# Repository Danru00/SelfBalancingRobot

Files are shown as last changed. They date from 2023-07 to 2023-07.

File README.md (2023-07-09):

# SelfBalancingRobot
Two-wheeled self-balancing robot realized for the Robotics course at Polito, academic year 2022-2023. The simulation is based on ROS Noetic and works on Ubuntu 20.04

# Run the Gazebo simulation
- Download the robot_assembly folder in your catkin workspace and run from a terminal: catkin_make
- Run from a terminal: roslaunch robot_assembly istagger_launch.launch
- After starting the simulation, the robot will initially fall. By rotating it upwards the PID controller will start working balancing the robot as prescribed
- You can tune the PID parameter by changing them in the Python file "pid_controller" under robot_assembly/src

# Run the Simscape simulation
- Download the Simscape folder
- Run the robot_assembly_simscape_DataFile in Matlab
- Open and run the robot_assembly.slx file to start the simulation
- You can tune the PID parameters changing them in the PID block

# Hardware implementation and Arduino code
Hardware details together with additional information on the project can be found in the Report_RoboticsProject_SelfBalancingRobot.pdf included in this repo.

The Arduino code can be uploaded through the Arduino IDE software and is intended for use on the Arduino Nano, but should also work with other similar boards. To correctly compile the program it is necessary to install the libraries linked at the beginning of the code by downloading them from GitHub and putting them under the Documents/Arduino/libraries folder.

Pin definitions in the code have to be changed depending on the connections with the driver and the motor. The IMU calibration offsets, PID parameters, and the unstable equilibrium position used for reference can also be changed in the program depending on the adopted hardware configuration.

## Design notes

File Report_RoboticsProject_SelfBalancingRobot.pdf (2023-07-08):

# POLITECNICO DI TORINO

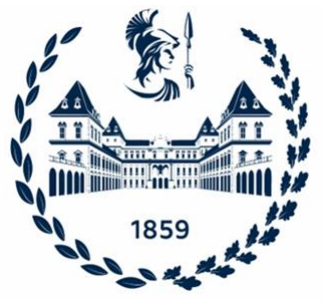
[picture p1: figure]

## Department of CONTROL AND COMPUTER

## ENGINEERING (DAUIN) Master Degree in Mechatronic Engineering

a.a. 2022/2023

## Robotics

## Prof. A. Rizzo

## T.A.: G. Galati and M. Rinaldi

## Self-balancing robot

## Aisa Filippo – 315421

## Musio Maria Grazia – 315756

## Russo Daniele – 308291

## Ursi Mariateresa – 315428

## Valenziano Gaia – 309918

## Contents

## Abstract

This project was aimed to design, simulate, build and study a self-balancing robot.
It is a two wheeled machine which stays in an unstable equilibrium and it returns to it after the application of a disturbance.

The research development started with a first theoretical and simplified model of the system. Then, a detailed and precise CAD model of the robot was created in SolidWorks.
Many simulations were performed: at first in Simscape to visualise the behaviour of the system; later, as soon as the performances were satisfactory, the robot was simulated in Gazebo and finally it was physically built.

The main trouble when designing a robot of this kind was the control system.
In this project a PID controller was chosen to implement a simple but effective and efficient control algorithm. The prototype was built with an IMU element to include a state estimation, which is important for the control system itself.

## Introduction

## Background

The working principle of a two wheeled self-balancing robot is similar to that of the human body, which can be seen as an inverted pendulum balancing the whole upper body around the ankles.
Although the self-balancing robots have advantages with respect to other robotic configurations, e.g. the mechanical simplicity, an accurate control could be very hard to be successfully achieved.

In order to maintain a balance, a gyroscope and accelerometer in form of Inertial Measurement Unit (IMU) is used. The latter provides the angle of fall of the robot that is then used by the PID controller to calculate the motor input required to track the constant reference angle corresponding to the unstable equilibrium position.
The signal is sent as PWM to the motors, increasing and decreasing the speed of the wheels and changing their directions when needed.

Inverted pendulum applications are plenty: in the recent decade, segways making use of bodily movements for steering have emerged on the market.
All these applications share with each other the position of the centre of mass above their pivot points, thus the requirement of active control for balancing.

## Purpose

The focus of this project is to build a simple working prototype of a two wheeled self-balancing robot, starting from the design of its mechanical structure and finishing with the code implementation that enables it to be balanced, at the end.

## Method

At the beginning preliminary research was conducted to correctly understand the system dynamics and the electronics behind. Thus, the dynamic equations were derived.
These equations were used to design a PID controller for stabilising the robot.
Once the model was precisely created in SolidWorks, it was exported and integrated in simulation platforms to emulate the real robot’s behaviour together with the developed control system before the effective construction.

## Theoretical approach

## System modelling

A self-balancing robot is typically modelled as an inverted pendulum.
In this project an even simple model was used at the beginning: an inverted pendulum which was balanced in the unstable equilibrium point through a PID controller.

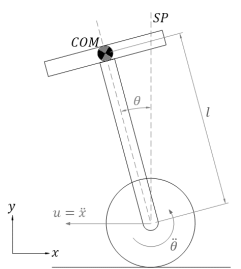
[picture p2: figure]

The equation of motion of the self-balancing robot was derived using Lagrange’s equations (inverted pendulum), by analysing the dynamics of the robot:

lθ¨ − gsinθ = x¨cosθ

Here, l is the distance of the center of mass of the robot from the axis of rotation (i.e. wheel centre), g is the acceleration due to gravity, θ is the pitch angle, θ¨ is the angular acceleration and x¨ is the linear acceleration (fed as control input u).

Then, the dynamics of the model was written as:

θ¨ =

g
l

sinθ +

u
l

cosθ

The state of the system was represented:
{

x1 = θ
x2 = θ˙

; x = [

x1
x2

]=[

θ
θ˙

]

Measuring the pitch angle θ of the robot:

output: y = θ

Figure 1 Dynamics of a Self-Balancing Robot

The control signal influenced the linear acceleration of the base of the robot, therefore:

control signal: u = x¨

Hence, we obtained the open-loop system dynamics:

x¨ = f(x, u) = [

θ˙
θ̈

] = [

x2
g
l

sinθ +

u
l

cosθ]; y = ℎ(x) = x1.

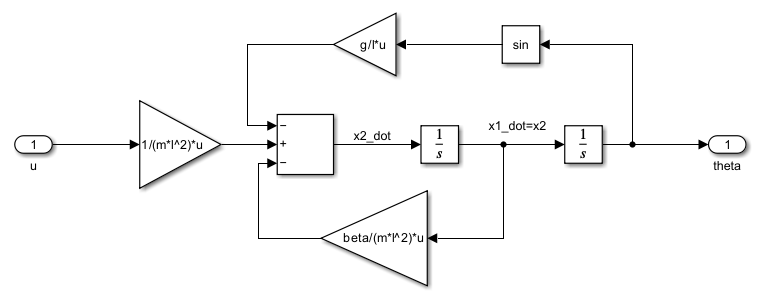
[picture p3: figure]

## Control system

As previously discussed, the control system was based on a PID controller.
It was chosen among many options, which also included LQ and MPC controllers, thanks to its simplicity and the ability to stabilise a system with a high unstable dynamic, maintaining the vertical position of the robot.

Figure 2 Dynamical system in Simulink

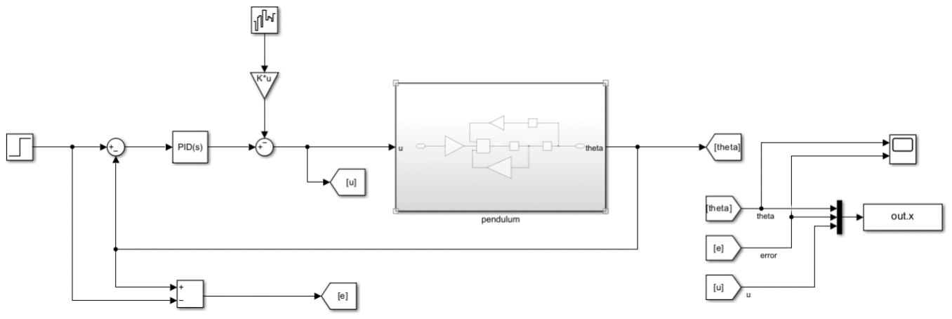
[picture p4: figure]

Figure 3 Closed-loop with PID controller

The primary objective of the PID controller is to maintain the value of the pitch angle θ of the robot close to the setpoint value, chosen to be 180° based on the IMU position on the robot, which is fed to the controller as a reference signal.
The error e(t) is computed through negative feedback, subtracting the feedback measurement from the setpoint. Thus, it is fed as input to the PID controller.
On the basis of Ki, Kp, and Kd controller gains, the input of the plant u(t) was computed:

u(t) = Kp ∗ e(t) + Ki ∗ ∫ e(t)dt

t

0

+

Kd ∗ de(t)
dt

The three control branches are weighted thanks to their gains and then summed together in order to achieve the required input of the plant.

The following explanation clarify the method used to tune those gains:
- Kp, the main task of the proportional part is to reduce the rise time, as well as the steady state error, but it increases the overshoot and generates an offset error;
- Kd, the derivative term increasesthe damping of the system by reducing the overshoot and the settling time, useful to smooth the behaviour of the system;
- Ki, the integral term is used to completely eliminate the steady state error, so it is useful when an offset error is generated by the system.
To summarise, the proportional term corrects the current errors, the integral term compensates the past errors, the derivative term avoids the future errors predicting them.

Tuning the PID controller gains is not done through any formula, but it is an empirical procedure based on the system behaviour, following a conventional order: proportional, integral and derivative, respectively. Hence, the integral removes the offset error generated by the proportional and the derivative smooths the system behaviour.
To reach a correct stabilisation, the tuning was done with the trial and error method on the Simscape simulation and then it was applied to the real robot.

## Simulation

At first the model of the robot was realized in SolidWorks and then exported through a plugin to use it in Matlab and perform the simulation through Simscape.
Moreover, the same CAD model was exported in URDF format through another plugin to be uploaded in ROS and simulated in Gazebo.

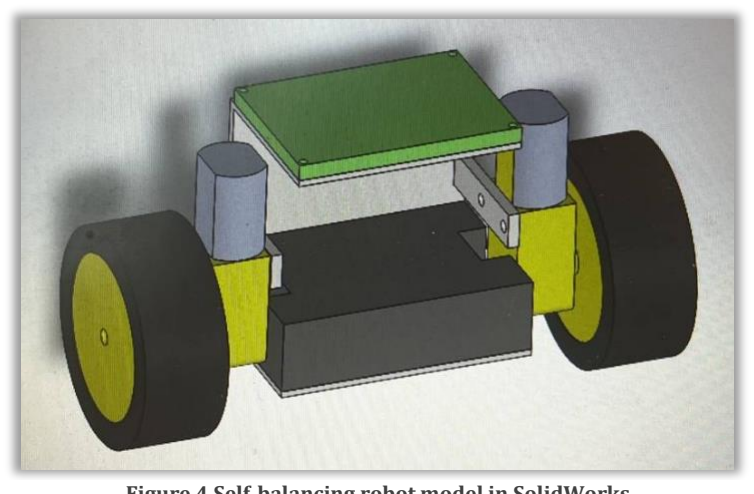
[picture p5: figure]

## Simulink and Simscape

Simscape is part of the larger MATLAB and Simulink software environment and uses a physical modelling approach to represent and simulate systems. It allows users to model and simulate a wide range of physical systems, including mechanical, electrical, hydraulic and thermal systems. It provides a library of pre-built components, such as motors, sensors, and actuators, that can be easily combined to create complex systems.
The simulation can be run and analysed using Simulink tools, such as scopes and data logging. Simscape also provides tools for analysing system performance, such as frequency response plots and transient analysis.

Our self-balancing robot was simulated in Simscape with the 3D CAD model of the real robot. Taking inspiration from other projects, the simulation was performed in Simscape by integrating the robot file obtained through the Simscape Multibody Link Simulink blocks to implement the control.

Thus, a PID controller was inserted and properly tuned. After, an initial perturbation was inserted to check the stability of the robot.

At the beginning, small arbitrary values were set as PID parameters to observe the behaviour in response to an applied disturbance. Then, step by step we tuned them, until the convergence to the equilibrium was achieved. The final values are shown in Figure 7.

Figure 4 Self-balancing robot model in SolidWorks

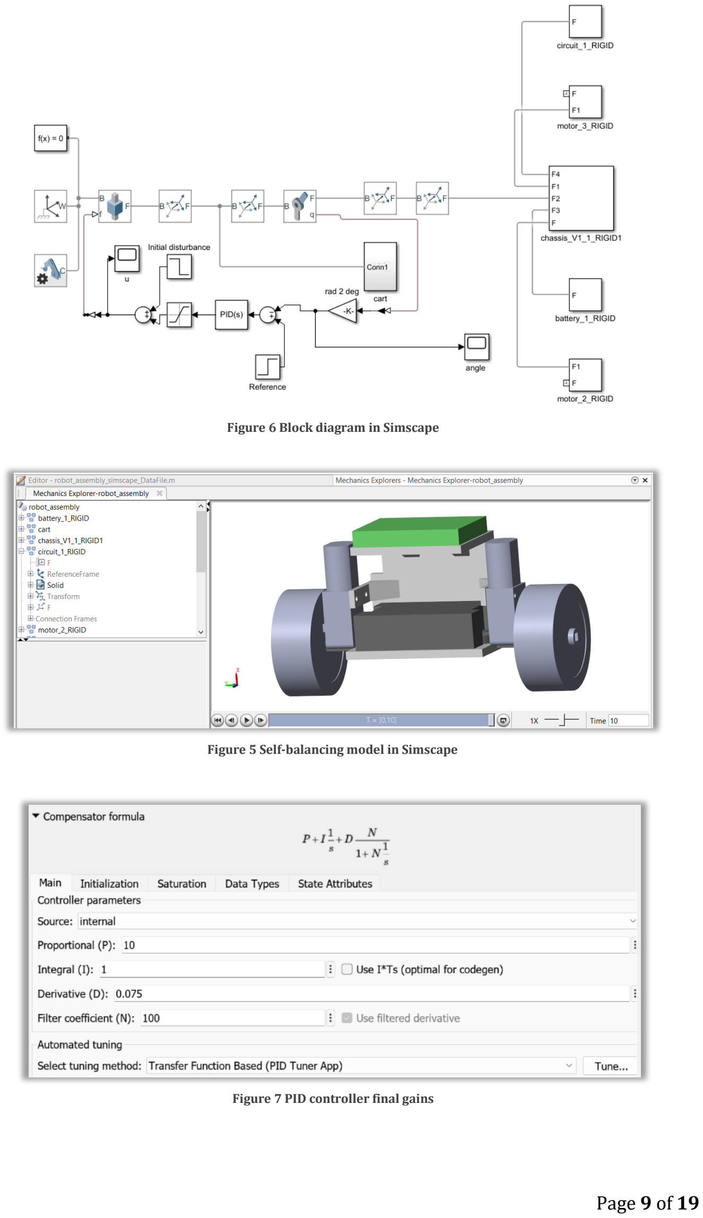
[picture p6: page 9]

Figure 6 Block diagram in Simscape

Figure 5 Self-balancing model in Simscape

Figure 7 PID controller final gains

## ROS and Gazebo

Gazebo is an open-source 3D simulator with the ability to simulate robot groups, sensors and various objects. Different types of objects can be loaded into the simulator, from simple shapes such as cubes and spheres to complex models as buildings or animals. Each object has its own characteristics: mass, speed, friction and numerous other physical and visualization properties in order to make the simulation as realistic as possible.

There is also a community-run robot database that everyone can use and modify as they please. Gazebo can also generate data from different sensors: laser rangefinder, 2D and RGB-D cameras, contact sensors, Inertial Measurement Units (IMU) and Radio Frequency IDentification (RFID). By connecting one or more sensors to a robot model, it’s possible to change the robot's actions based on the data generated by the sensors.
For this reason, it is possible to implement custom plugins that manage the data collected by the sensors and that control any aspect of the robot.

## Folders organization

A new workspace called barcollo was created. It contains three folders: besides build and devel, one can focus particularly on the 3rd one that is the src folder. The latter contains the package of interest called robot_assembly, which in turn presents other folders among which the most important and essential for a clear comprehension are mentioned below.

## URDF structure (urdf folder)

URDF (Unified Robot Description Format) is an XML format used in ROS for representing robot models. The description of the model consists of defining two main sets, one of links and the other referred to the joints. A link describes the characteristics of a rigid body with inertia, while a joint the kinematics and dynamics of the robot, allowing the relative motion of links.

Our self-balancing robot’s URDF was directly exported from SolidWorks.
It is mainly composed by:
- Links: base_link, RightWheelLink, LeftWheelLink
- Joints: RightWheelJoint, LeftWheelJoint - representative of both left and right robot’s wheels actuated by two motors.

The two wheels were modelled as continuous jointsrotating about a pre-determined axis: the z-axes were defined in opposite direction with each other due to the symmetry between the two wheels, without specifying any upper and lower limit.

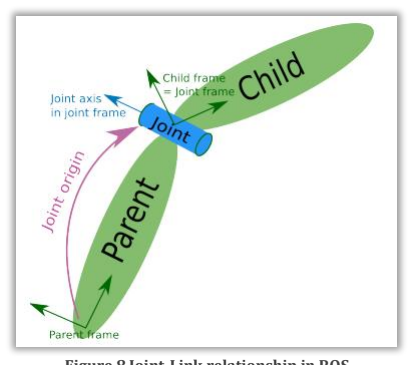
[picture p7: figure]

Moreover, two plugins were added to the URDF file, to enhance the capabilities of the URDF models by enabling dynamic behaviour, sensor simulation, ROS integration, and custom functionality. They bridge the gap between the static robot description in URDF and the dynamic simulation environment in Gazebo, allowing a more realistic and interactive simulations.

Particularly, in this project imu_plugin and gazebo_ros_control were used:

- “imu_plugin” - to simulate an Inertial Measurement Unit (IMU) sensor. It provides a way to incorporate sensor models and simulate sensor data in Gazebo, including cameras, depth sensors, lidars, inertial measurement units (IMUs) and so on, so forth. Sensor plugin generates realistic sensor data based on the simulated environment and robot interactions, allowing to develop and test the perception algorithms using the simulated sensor inputs.
- “gazebo_ros_control” - responsible for integrating the ROS control system with Gazebo. It enables the communication between the simulated robot and the ROS environment. This plugin can publish and subscribe to ROS topics, providing a way to exchange data between Gazebo and other ROS nodes.

To define the mechanical relationships, control interfaces and effort/torque simulation between actuators and joints, transmissions were added in URDF. They enable accurate motion simulation, control behaviour and consistency between the robot's description and its visual representation in Gazebo, again facilitating realistic and reliable robot simulations.

Two transmissions were used, left_wheel_trans and right_wheel_trans, defining simple transmissions between joints and actuators, the motor _left and motor _right, respectively.

Then, three gazebo reference blocks were included, one for each link, just to set the colour and the friction coefficients for the two wheels and the base_link.

Figure 8 Joint-Link relationship in ROS

## .yaml file (config folder)

The PID gains and controller settings have been saved in the controller.yaml file that gets loaded to the ROS Parameter Server via the launch file. It allowed to set up two velocity controllers for both the left and right wheel joints of the robot in simulation. These controllers use PID control to regulate the joint velocities based on the desired values and the feedback received from the joint_state_controller.

By adjusting the PID gains Kp, Ki and Kd, the controller's performance could be fine-tuned, ideally achieving stable and accurate velocity control.

## .launch files (launch folder)

The gazebo.launch and istagger_launch.launch files set up the Gazebo simulation environment for the whole robot_assembly package including the robot controllers.
In particular, they contain the reference for the URDF model file, the loading functionality to specify the needed parameters inside the controller.yaml file and they spawn the robot both in Rviz and Gazebo simulation environments.

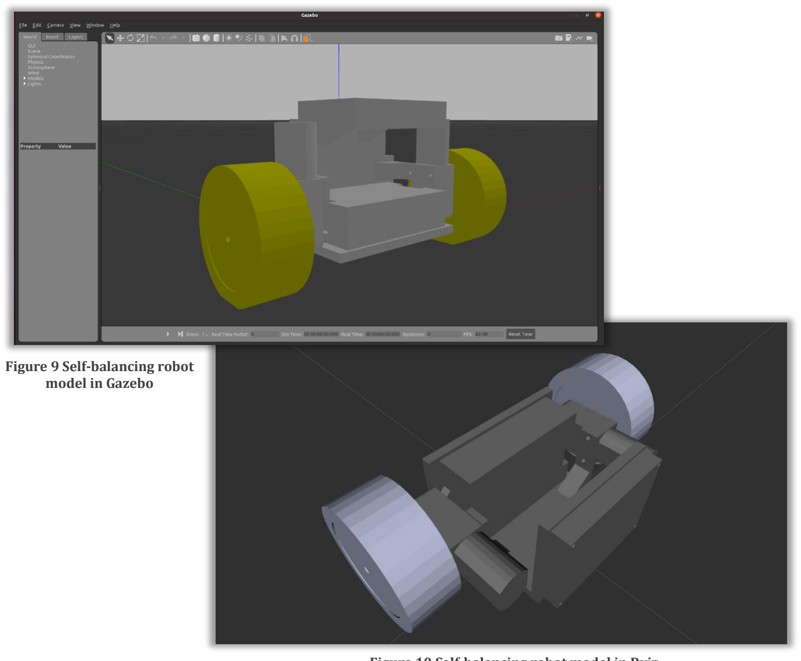
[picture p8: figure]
Figure 9 Self-balancing robot model in Gazebo

Figure 10 Self-balancing robot model in Rviz

## ROS node: Publisher/Subscriber (src folder)

To implement the required PID controller a node was written in Python: pid_controller.py:

- Two publishers, publish velocity commands to the robot’s right and left wheels;
- A function imu_elaboration is called when the IMU sensor data is received: it extracts the quaternion orientation from the IMU message and passes it to quat2pitch function to obtain the pitch angle. The latter is then used to calculate the velocity correction using a PI controller, which finally is returned as the output;
- PidGenerator class represents a PID controller, initialised with the three PID gains Kp, Ki and Kd. This class provides a method getCorrection to compute the velocity correction based on the current error and the target value. The tune method is included to dynamically update the PID gains;
- A callback function for the IMU subscriber receives the IMU data and passes it to imu_elaboration to obtain the velocity correction. The latter is then published to the right and left wheel velocity controllers;
- PidController is the main function of the script: it initialises the ROS node, sets up the Subscriber for IMU data and enters the ROS spin loop to process incoming messages.

## Simulation in Gazebo: comments and results

The simulation was successfully performed. It’s worth to notice that the PID gains set for the simulation are the same as the ones used for controlling the robot made of PLA, that is 1

st
prototype constructed: Kp=10, Kd=5, Ki=0.075. Thus, the resulting behaviour of the simulated self-balancing robot in Gazebo was coherent with the real one.

## Prototyping and testing

## Components

After the modelling and simulation phases, a prototype of the self-balancing robot was built with the following components:

- Arduino Nano
- IMU GY-521
- Motor driver TB6612FNG
- 50x70 PCB stripboard
- DC-DC motors x2
- 7.2 V battery
- Wheels
- Wires
- Chassis

The PCB (Printed Circuit Board) was built and manually soldered in laboratory, while the chassis was 3D printed from the CAD model.

## Mechanical systems

The chassis structure was designed after choosing the components. It has two layers: the one below to host the power supply and the other above for the on-board electronics.
The actuators were fixed with screws to support the vertical part of the chassis.
The wheels were connected to the motors’ shafts, again using screws.

## Electrical system

## Power supply

The entire on-board electronics and actuators are powered using a 7.2 V Lithium battery pack. This power supply was chosen in order to be able to supply the whole electronic and actuators for a prolonged duration.

## Inertial Measurement Unit (IMU)

The whole self-balancing procedure is based on the measurements of the robot’s position, hence the IMU is probably the fundamental electronical element for this project.
The IMU used is a GY-521, 6 DOF. It combines an accelerometer and gyroscope and MPU-6050 (Arduino Playground). The criticality of the IMU is that it is very noisy, but the data were considered good enough for our project.

## Microcontroller

The on-board electronic is all controlled by an Arduino Nano. It was chosen because it is compact and light, besides the open-source nature of the hardware.
Moreover, it is compatible with the IMU thanks to its I2C supported communication and it is easily connectable to the motor driver used. The computational resolution of this microcontroller is enough for the use case.

## Motor driver and actuators

A TB6612FNG driver was chosen in order to correctly drive the two motors from the power supply and to translate the PWM (Power Width Modulation) signals in speed regulation, capability that was essential for the success of the project. Due to their simplicity and cost-effectiveness, a decision was made to opt for two 2 kg-m DC motors operating at 500 rpm. Other actuators, such as stepper or servo, could give better feedback, but since it was chosen not to control the position of the robot, they were not necessary.

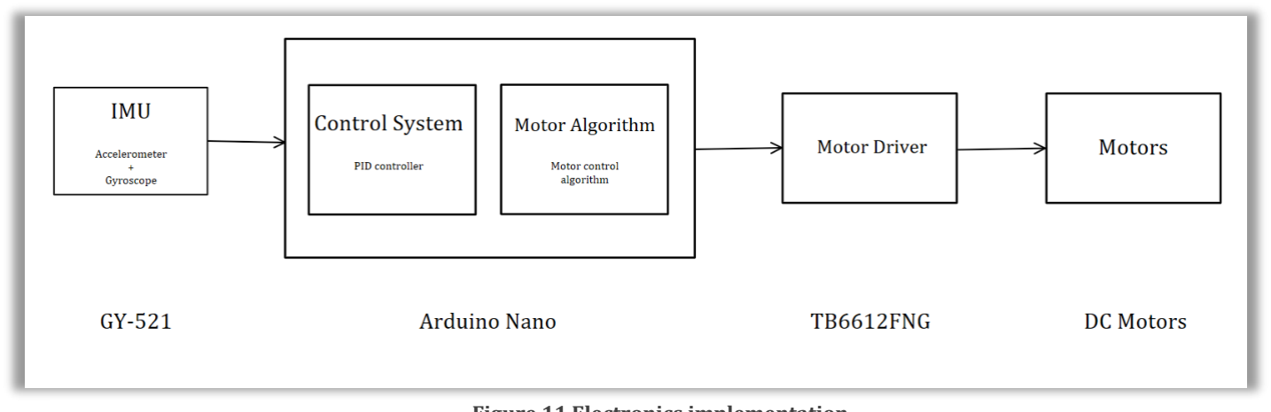
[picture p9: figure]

The self-balancing principle of the system is accomplished thanks to the help of the IMU, in particular the MPU-6050 sensor. Since the robot has only 1 DOF, three angle are measured by the gyro but only the yaw value is considered and processed by the microcontroller to calculate the PWM signal.

Figure 11 Electronics implementation

The tilt angle (yaw value) is compared against the required setpoint producing the error in position. The latter isfed to the PID controller, then its output is mapped between [–225, 225] and sent to the motor control algorithm. Thus, it is used to generate the PWM signal to be sent to the driver which translates it in the current, needed to maintain the robot in the upright position.

## Files and code implementation

CAD, simulations and the Arduino control program can be found on the GitHub repository of the project together with some instructions on how to replicate the results:

https://github.com/Danru00/SelfBalancingRobot-BarcolloMaNonMollo

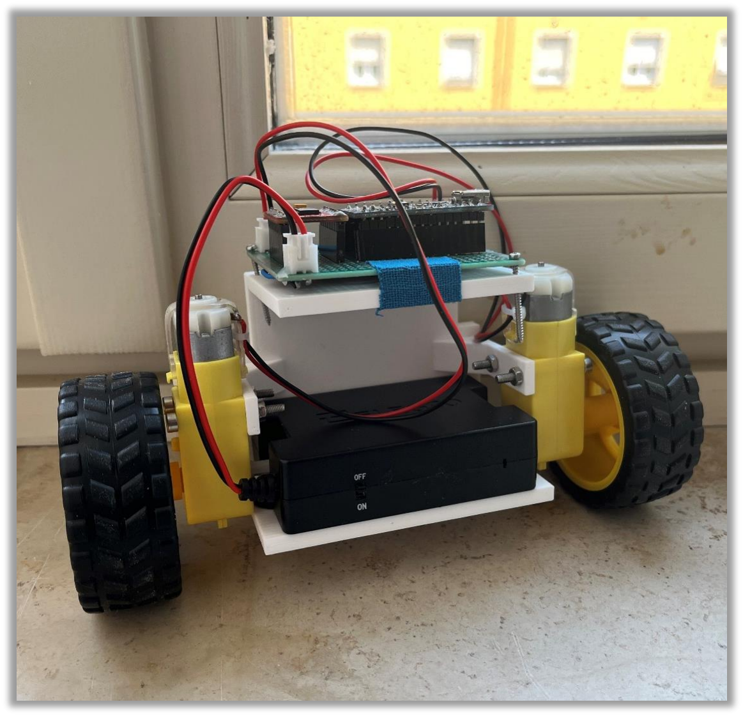
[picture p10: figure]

Figure 12 First working prototype of the self-balancing robot

## Results and discussion

From the performance analysis of the robot, the most significant parameters were discovered: they are responsible of the behaviour of the whole system.

## Controller gains

The controller gains, Kp, Ki, Kd are responsible for the PID response to the error between the setpoint and the feedback position. During the first MATLAB simulation they were chosen using the PID tuner app. Applying these values in both Simscape and Gazebo simulations, the robot was not working as well due to the differences in the systems, so different parameters were chosen by experimentally tuning them.
The same empirical procedure was used to set the parameters for the prototype, verifying the consistency between the values used in Gazebo and those ones in the real robot.

## Moment of inertia of the robot

The moment of inertia of the robot changes varying the height and the mass distribution of the robot. In this system, knowing that the angular acceleration is inversely proportional to the moment of inertia of the body, it was chosen to put most of the weight in correspondence of the wheels to reduce the inertia at its minimum.
This decision was taken in order to minimize the effort of the actuators.

## IMU Parameters

The calibration of the IMU is fundamental for the system. Since it gets very noisy signals due to its nature, its positioning on the prototype was chosen to avoid disturbances from the wheels and it was also soldered directly on the PCB board to bypass additional vibrations. An initial calibration was needed to find the component’s specific offsets to insert into the control program running on the Arduino Nano.

## Future implementation

Knowing the imperfections of the first prototype, the next one would have differences in both the structure and components. For instance, more precise actuators can help to get a more accurate behaviour during the stabilising transient. As said above, the IMU signals are very noisy, so a filter in the code (e.g. Kalman filter) could be used to tackle bad components in the signal which cause unprecise wheels moments. Furthermore, a higher chassis could be experimented: the inertia would increase, requiring bigger effort from the motor, but at the same time the disturbances on the IMU should decrease (due to less tilting) and control performance should increase.

## Conclusions

The self-balancing robot project was ideated to apply key concepts of mechanics, electronics, robotics and control theory in order to learn how to use these knowledges horizontally.
The performance of the robot is not so perfect because of the limitations linked to the components; however it reached the expected and quite satisfying results.
Surely a second prototype with the described improvements would get more precise results. It is interesting to note that PID parameters found to be working in Simscape or Gazebo simulations are equal or really close to the parameters actually working on the real prototype.

Future developments on the system could be position control of the robot, autonomous features such as path planning, obstacle avoidance, perimeter following and so on.

## References

Inspiration for the Simscape Simulation: https://it.mathworks.com/matlabcentral/fileexchange/88768-two-wheeled-self-balancingrobot (https://it.mathworks.com/matlabcentral/fileexchange/88768-two-wheeled-self-balancing-robot)

Solidworks to URDF exporter:
http://wiki.ros.org/sw_urdf_exporter

Simscape Multibody Link plugin: https://it.mathworks.com/help/smlink/ref/linking-and-unlinking-simmechanics-link-software-with-solidworks.html (https://it.mathworks.com/help/smlink/ref/linking-and-unlinking-simmechanics-link-software-with-solidworks.html)

Inspiration for the structure and Arduino control algorithm: https://circuitdigest.com/microcontroller-projects/arduino-based-self-balancing-robot

Inspiration for the Gazebo simulation: https://github.com/sezan92/self_balancing_robot

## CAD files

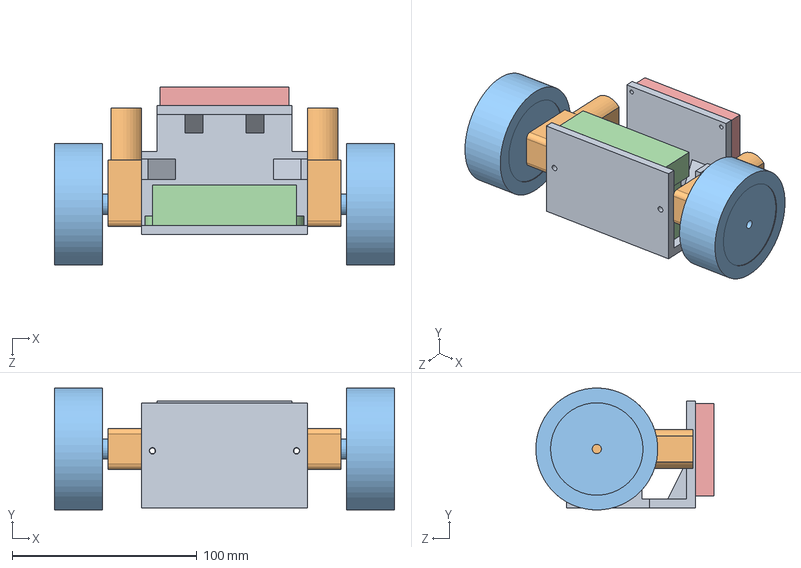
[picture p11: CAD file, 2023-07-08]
CAD/robot_assembly.SLDASM
184.0 x 65.9 x 96.5 mm
chassis_V1
motor x 2
wheel x 2
battery
circuit

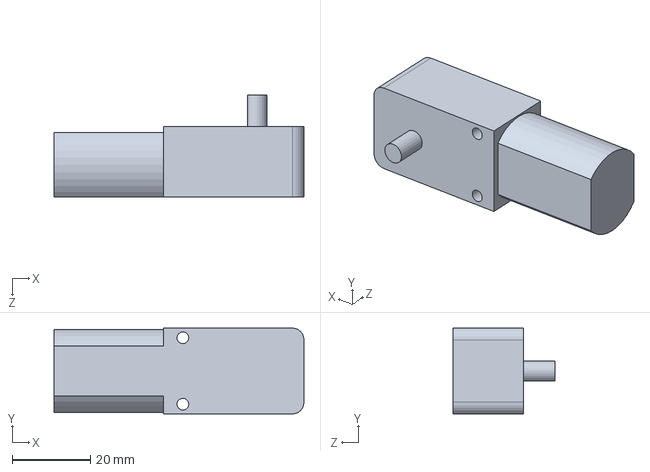
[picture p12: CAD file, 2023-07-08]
CAD/motor.SLDPRT
64.0 x 22.0 x 26.0 mm

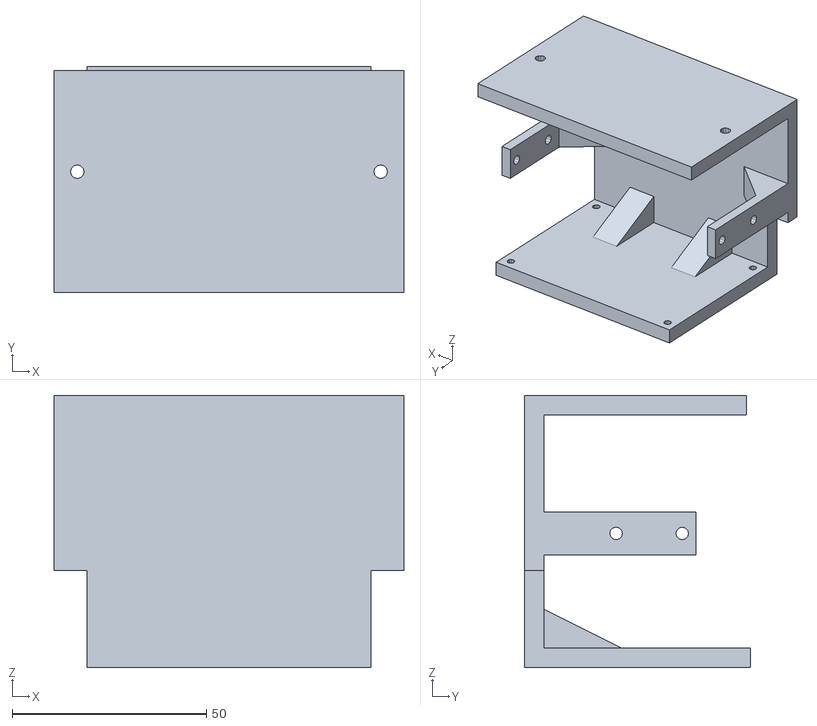
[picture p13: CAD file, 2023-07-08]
CAD/STL/chassis.STL
90.0 x 58.0 x 70.0

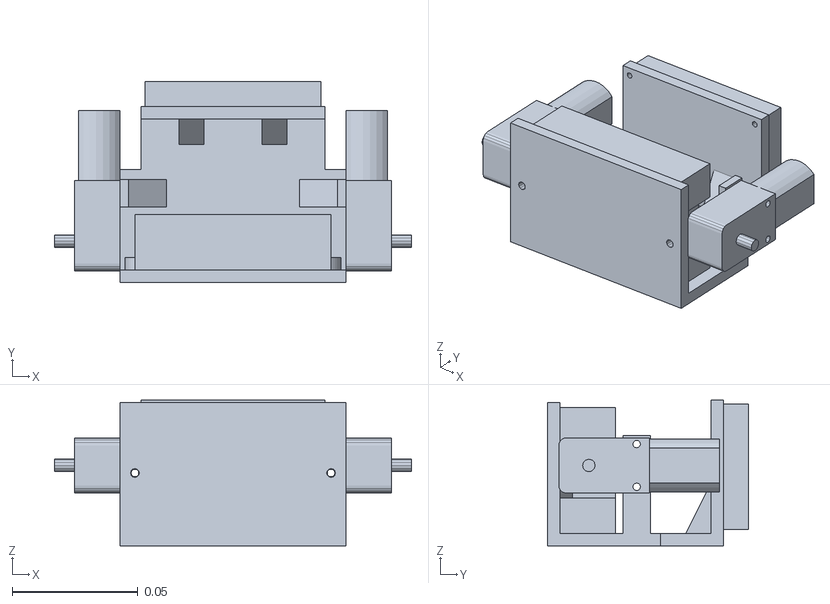
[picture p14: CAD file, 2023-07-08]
CAD/URDF_Tool_Export/robot_assembly.SLDASM/meshes/base_link.STL
0.142 x 0.08 x 0.058

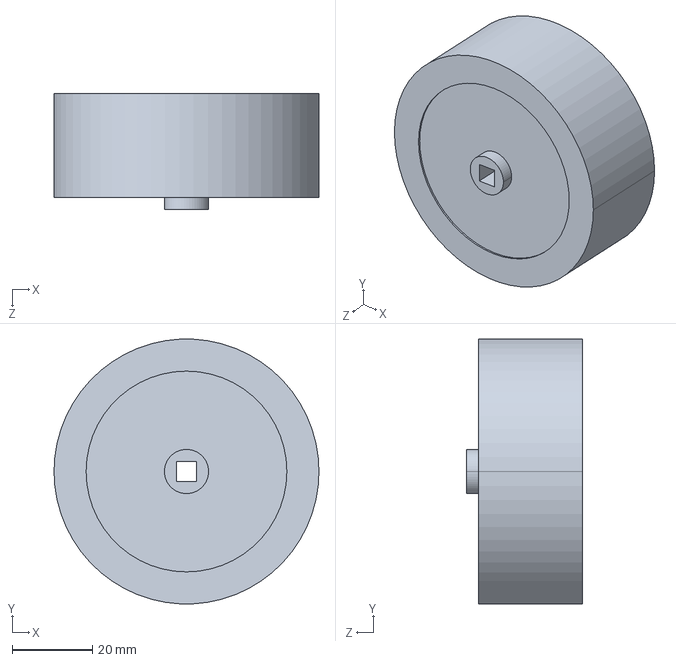
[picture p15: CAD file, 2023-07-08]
Simscape/wheel_Default_sldprt.STEP
66.0 x 65.9 x 29.0 mm

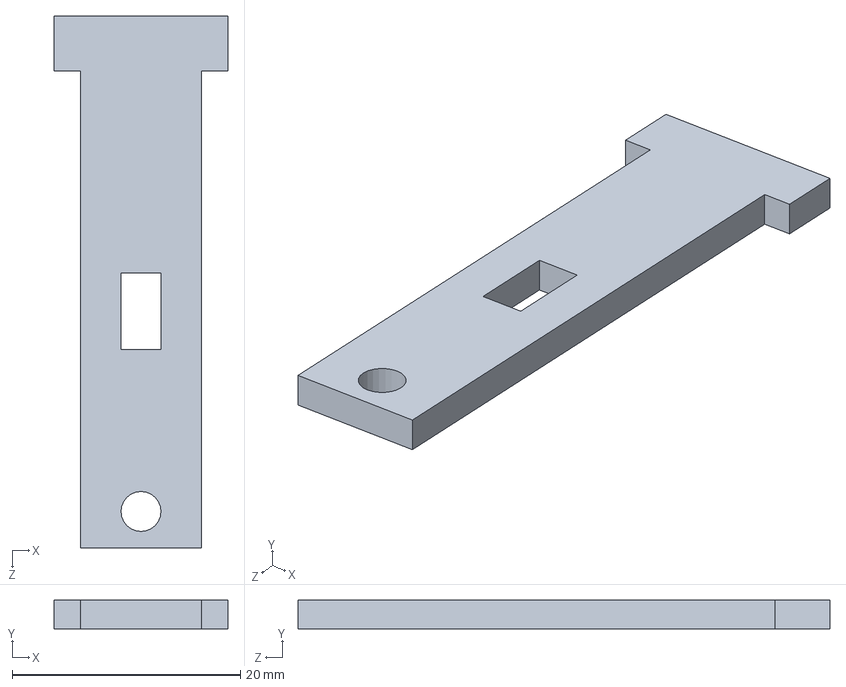
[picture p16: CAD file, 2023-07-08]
CAD/Motor_mount.SLDPRT
15.2 x 2.50 x 46.6 mm

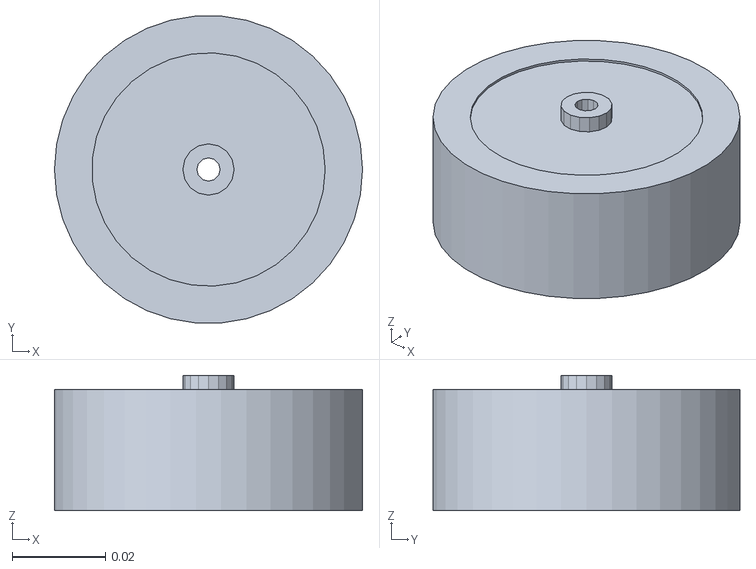
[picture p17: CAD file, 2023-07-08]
CAD/URDF_Tool_Export/robot_assembly.SLDASM/meshes/RightWheelLink.STL
0.066 x 0.0658 x 0.029

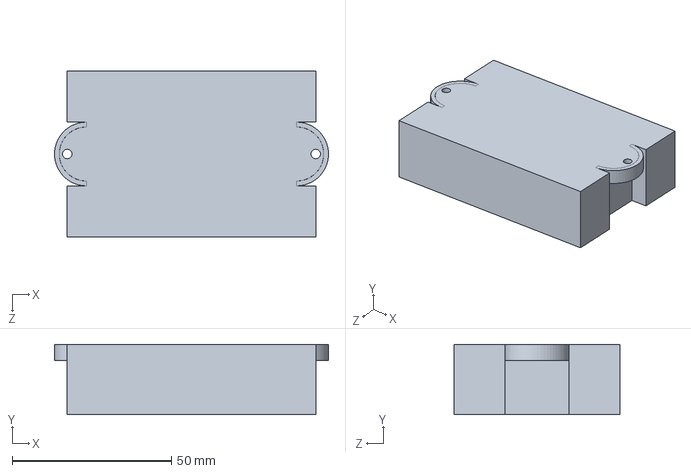
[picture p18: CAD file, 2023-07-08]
CAD/battery.SLDPRT
86.0 x 22.0 x 52.0 mm

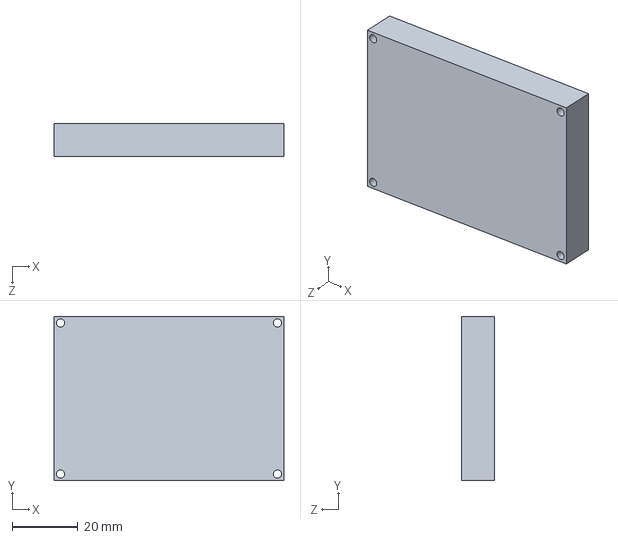
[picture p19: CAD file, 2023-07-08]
CAD/circuit.SLDPRT
70.0 x 50.0 x 10.0 mm

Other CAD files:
Simscape/chassis_V1_Default_sldprt.STEP
CAD/URDF_Tool_Export/robot_assembly.SLDASM/meshes/LeftWheelLink.STL
Simscape/motor_Default_sldprt.STEP
Simscape/battery_Default_sldprt.STEP
Simscape/circuit_Default_sldprt.STEP
CAD/wheel.SLDPRT
CAD/chassis_V1.SLDPRT

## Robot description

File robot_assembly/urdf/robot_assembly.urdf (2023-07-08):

<?xml version="1.0" encoding="utf-8"?>

<robot name="robot_assembly">
  
  <link name="base_link">
    
    <visual>
      <origin xyz="0 0 0" rpy="0 0 0" />
      <geometry>
        <mesh filename="package://robot_assembly/meshes/base_link.STL" />
      </geometry>
      <material name="">
        <color rgba="0.501960784313725 0.501960784313725 0.501960784313725 1" />
      </material>
    </visual>
    <collision>
      <origin xyz="0 0 0" rpy="0 0 0" />
      <geometry>
        <mesh filename="package://robot_assembly/meshes/base_link.STL" />
      </geometry>
    </collision>
  </link>

  <link name='base_inertial'>
    <inertial>
      <origin xyz="0 0 0.0320025" rpy="0 0 0" />
      <mass value="0.26433" />
      <inertia ixx="0.00015" ixy="1e-20" iyx="ixy" ixz="1e-20" izx="ixz" iyy="0.0002" iyz="1e-20" izy="iyz" izz="0.000175" />
    </inertial>
  </link>

  <link name="RightWheelLink">
    <inertial>
      <origin xyz="0 0 -0.015957" rpy="0 0 0" />
      <mass value="0.086761" />
      <inertia ixx="2.5E-05" ixy="0" ixz="0" iyy="2.5E-05" iyz="0" izz="5E-05" />
    </inertial>
    <visual>
      <origin xyz="0 0 0" rpy="0 0 0" />
      <geometry>
        <mesh filename="package://robot_assembly/meshes/RightWheelLink.STL" />
      </geometry>
      <material name="">
        <color rgba="0.79216 0.81961 0.93333 1" />
      </material>
    </visual>
    <collision>
      <origin xyz="0 0 -0.015957" rpy="0 0 0" />
      <geometry>
        <cylinder radius="${0.066/2}" length="0.022"/> 
      </geometry>
    </collision>
  </link>
  
  <joint name="RightWheelJoint" type="continuous">
    <origin xyz="-0.063 -0.0185 0.032" rpy="-1.5708 -1.257 -1.5708" />
    <parent link="base_link" />
    <child link="RightWheelLink" />
    <axis xyz="0 0 1" />
   <limit effort="100" velocity="100" />
   <dynamics damping="0.7" friction="0.5" />
  </joint>

  <joint name="FixedInertial" type="fixed">
    <origin xyz="0 0 0" rpy="0 0 0" />
    <parent link="base_link" />
    <child link="base_inertial" />
  </joint>
  
  <link name="LeftWheelLink">
    <inertial>
      <origin xyz="0 0 -0.015957" rpy="0 0 0" />
      <mass value="0.086761" />
      <inertia ixx="2.5E-05" ixy="0" ixz="0" iyy="2.5E-05" iyz="0" izz="5E-05"/>
    </inertial>
    <visual>
      <origin xyz="0 0 0" rpy="0 0 0" />
      <geometry>
          <mesh filename="package://robot_assembly/meshes/LeftWheelLink.STL" /> 
      </geometry>
      <material name="">
        <color rgba="0.79216 0.81961 0.93333 1" />
      </material>
    </visual>
    <collision>
      <origin xyz="0 0 -0.015957" rpy="0 0 0" />
      <geometry>
         <cylinder radius="${0.066/2}" length="0.022"/> 
      </geometry>
    </collision>
  </link>
  
  <joint name="LeftWheelJoint" type="continuous">
    <origin xyz="0.063 -0.0185 0.032" rpy="-1.5708 -1.257 1.5708" />
    <parent link="base_link" />
    <child link="LeftWheelLink" />
    <axis xyz="0 0 -1" />
    <limit effort="100" velocity="100" />
     <dynamics damping="0.7" friction="0.5" />
  </joint>



	 <gazebo>
		<plugin name="imu_plugin" filename="libgazebo_ros_imu.so">
			<alwaysOn>true</alwaysOn>
			<bodyName>base_link</bodyName>
			<topicName>imu</topicName>
			<serviceName>imu_service</serviceName>
			<gaussianNoise>0.0</gaussianNoise>
			<rpyOffsets>0 0 0</rpyOffsets>
			<accelDrift>0.5 0.5 0.5</accelDrift>
			<accelGaussianNoise>0 0 0</accelGaussianNoise>
			<rateDrift>0.0 0.0 0.0</rateDrift>
        	<rateGaussianNoise>0.00 0.00 0.00</rateGaussianNoise>
        	<headingDrift>0.0</headingDrift>
        	<headingGaussianNoise>0.00</headingGaussianNoise>
			<updateRate>100.0</updateRate>
		</plugin>
	</gazebo> 



  <transmission name="right_wheel_trans">
    <type>transmission_interface/SimpleTransmission</type>
    <joint name="RightWheelJoint">
      <hardwareInterface>hardware_interface/VelocityJointInterface</hardwareInterface>
    </joint>
    <actuator name="motor_right">
      <mechanicalReduction>1</mechanicalReduction>
    </actuator>
  </transmission>

  <transmission name="left_wheel_trans">
    <type>transmission_interface/SimpleTransmission</type>
    <joint name="LeftWheelJoint">
    <hardwareInterface>hardware_interface/VelocityJointInterface</hardwareInterface>
    </joint>
    <actuator name="motor_left">
      <mechanicalReduction>1</mechanicalReduction>
    </actuator>
  </transmission> 



  <gazebo reference= "LeftWheelLink" >
		<mu1>0.90</mu1>
		<mu2>0.65</mu2>
		<kp>100000</kp>
		<kd>10</kd>
		<material>Gazebo/Yellow</material> 
  </gazebo>
  
  <gazebo reference= "RightWheelLink" >
		<mu1>0.90</mu1>
		<mu2>0.65</mu2>
		<kp>100000</kp>
		<kd>10</kd>
		<material>Gazebo/Yellow</material> 
  </gazebo>
  
  <gazebo reference= "base_link" >
		<material>Gazebo/White</material>
  </gazebo>



 <gazebo>
    <plugin name="gazebo_ros_control" filename="libgazebo_ros_control.so">
     <robotNamespace>/robot_assembly</robotNamespace>
    </plugin>
 </gazebo> 


</robot>

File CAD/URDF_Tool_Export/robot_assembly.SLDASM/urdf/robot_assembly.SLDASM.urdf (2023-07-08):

<?xml version="1.0" encoding="utf-8"?>
<!-- This URDF was automatically created by SolidWorks to URDF Exporter! Originally created by Stephen Brawner (brawner@gmail.com) 
     Commit Version: 1.6.0-4-g7f85cfe  Build Version: 1.6.7995.38578
     For more information, please see http://wiki.ros.org/sw_urdf_exporter -->
<robot name="robot_assembly.SLDASM">
  <link name="base_link">
    <inertial>
      <origin xyz="3.2814E-18 0.026189 0.001556" rpy="0 0 0" />
      <mass value="0.26433" />
      <inertia ixx="0.00015157" ixy="2.1101E-20" ixz="2.5808E-20" iyy="0.00020961" iyz="-1.0564E-06" izz="0.0001781" />
    </inertial>
    <visual>
      <origin xyz="0 0 0" rpy="0 0 0" />
      <geometry>
        <mesh filename="package://robot_assembly.SLDASM/meshes/base_link.STL" />
      </geometry>
      <material name="">
        <color rgba="1 1 1 1" />
      </material>
    </visual>
    <collision>
      <origin xyz="0 0 0" rpy="0 0 0" />
      <geometry>
        <mesh filename="package://robot_assembly.SLDASM/meshes/base_link.STL" />
      </geometry>
    </collision>
  </link>
  <link name="RightWheelLink">
    <inertial>
      <origin xyz="-6.9389E-18 -4.8572E-17 -0.015957" rpy="0 0 0" />
      <mass value="0.086761" />
      <inertia ixx="2.8632E-05" ixy="1.6941E-21" ixz="-3.3692E-21" iyy="2.8632E-05" iyz="-1.2838E-20" izz="4.7824E-05" />
    </inertial>
    <visual>
      <origin xyz="0 0 0" rpy="0 0 0" />
      <geometry>
        <mesh filename="package://robot_assembly.SLDASM/meshes/RightWheelLink.STL" />
      </geometry>
      <material name="">
        <color rgba="0.79216 0.81961 0.93333 1" />
      </material>
    </visual>
    <collision>
      <origin xyz="0 0 0" rpy="0 0 0" />
      <geometry>
        <mesh filename="package://robot_assembly.SLDASM/meshes/RightWheelLink.STL" />
      </geometry>
    </collision>
  </link>
  <joint name="RightWheelJoint" type="continuous">
    <origin xyz="-0.063 -0.0185 0.032" rpy="-1.5708 -1.257 -1.5708" />
    <parent link="base_link" />
    <child link="RightWheelLink" />
    <axis xyz="0 0 1" />
  </joint>
  <link name="LeftWheelLink">
    <inertial>
      <origin xyz="0 0 0" rpy="0 0 0" />
      <mass value="0" />
      <inertia ixx="0" ixy="0" ixz="0" iyy="0" iyz="0" izz="0" />
    </inertial>
    <visual>
      <origin xyz="0 0 0" rpy="0 0 0" />
      <geometry>
        <mesh filename="package://robot_assembly.SLDASM/meshes/LeftWheelLink.STL" />
      </geometry>
      <material name="">
        <color rgba="1 1 1 1" />
      </material>
    </visual>
    <collision>
      <origin xyz="0 0 0" rpy="0 0 0" />
      <geometry>
        <mesh filename="package://robot_assembly.SLDASM/meshes/LeftWheelLink.STL" />
      </geometry>
    </collision>
  </link>
  <joint name="LeftWheelJoint" type="continuous">
    <origin xyz="0.063 -0.0185 0.032" rpy="-1.5708 -1.1445 1.5708" />
    <parent link="base_link" />
    <child link="LeftWheelLink" />
    <axis xyz="0 0 1" />
  </joint>
</robot>

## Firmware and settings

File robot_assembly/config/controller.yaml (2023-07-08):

robot_assembly:

  joint_state_controller:
    type: joint_state_controller/JointStateController
    publish_rate: 50
    
  lw_velocity_controller:
    type: velocity_controllers/JointVelocityController
    joint: LeftWheelJoint
    publish_rate: 50
    pid: {p: 10, i: 20, d: 0.075}

  rw_velocity_controller:
    type: velocity_controllers/JointVelocityController
    joint: RightWheelJoint
    publish_rate: 50
    pid: {p: 10, i: 20, d: 0.075}

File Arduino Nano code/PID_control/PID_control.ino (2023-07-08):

#include "I2Cdev.h" //https://github.com/jrowberg/i2cdevlib
#include <PID_v1.h> //From https://github.com/br3ttb/Arduino-PID-Library/
#include "MPU6050_6Axis_MotionApps20.h" //https://github.com/jrowberg/i2cdevlib/tree/master/Arduino/MPU6050

MPU6050 mpu;

// MPU control/status vars

bool dmpReady = false;  // set true if DMP init was successful

uint8_t mpuIntStatus;   // holds actual interrupt status byte from MPU

uint8_t devStatus;      // return status after each device operation (0 = success, !0 = error)

uint16_t packetSize;    // expected DMP packet size (default is 42 bytes)

uint16_t fifoCount;     // count of all bytes currently in FIFO

uint8_t fifoBuffer[64]; // FIFO storage buffer


// orientation/motion vars

Quaternion q;           // [w, x, y, z]         quaternion container

VectorFloat gravity;    // [x, y, z]            gravity vector

float ypr[3];           // [yaw, pitch, roll]   yaw/pitch/roll container and gravity vector


// Robot parameters to be tuned
 
double setpoint= 194; //set the value when the bot is perpendicular to ground using serial monitor. 

double Kp = 10; 

double Ki = 20; 

double Kd = 0.075; 





double input, output;

PID pid(&input, &output, &setpoint, Kp, Ki, Kd, DIRECT);



volatile bool mpuInterrupt = false;     // indicates whether MPU interrupt pin has gone high

void dmpDataReady()

{

    mpuInterrupt = true;

}

#define PWM1 9
#define AIN1 6
#define AIN2 7
#define PWM2 10
#define BIN1 4
#define BIN2 3

void setup() {

  Serial.begin(115200);


  // initialize device

    Serial.println(F("Initializing I2C devices..."));

    mpu.initialize();


     // verify connection

    Serial.println(F("Testing device connections..."));

    Serial.println(mpu.testConnection() ? F("MPU6050 connection successful") : F("MPU6050 connection failed"));


    // load and configure the DMP

    devStatus = mpu.dmpInitialize();


    

    // supply your own gyro offsets here, scaled for min sensitivity

    mpu.setXGyroOffset(310);

    mpu.setYGyroOffset(-76);

    mpu.setZGyroOffset(2);

    mpu.setZAccelOffset(734); 


      // make sure it worked (returns 0 if so)

    if (devStatus == 0)

    {

        // turn on the DMP, now that it's ready

        Serial.println(F("Enabling DMP..."));

        mpu.setDMPEnabled(true);


        // enable Arduino interrupt detection

        Serial.println(F("Enabling interrupt detection (Arduino external interrupt 0)..."));

        attachInterrupt(0, dmpDataReady, RISING);

        mpuIntStatus = mpu.getIntStatus();


        // set our DMP Ready flag so the main loop() function knows it's okay to use it

        Serial.println(F("DMP ready! Waiting for first interrupt..."));

        dmpReady = true;


        // get expected DMP packet size for later comparison

        packetSize = mpu.dmpGetFIFOPacketSize();

        

        //setup PID

        pid.SetMode(AUTOMATIC);

        pid.SetSampleTime(10);

        pid.SetOutputLimits(-255, 255);  

    }

    else

    {

        // ERROR!

        // 1 = initial memory load failed

        // 2 = DMP configuration updates failed

        // (if it's going to break, usually the code will be 1)

        Serial.print(F("DMP Initialization failed (code "));

        Serial.print(devStatus);

        Serial.println(F(")"));

    }



//Initialise the Motor output pins

    pinMode(PWM1,OUTPUT);
    pinMode(AIN1,OUTPUT);
    pinMode(AIN2,OUTPUT);
    pinMode(PWM2,OUTPUT);
    pinMode(BIN1,OUTPUT);
    pinMode(BIN2,OUTPUT);

    pinMode (5, OUTPUT);


//By default turn off both the motors

    digitalWrite(AIN1,LOW);

    digitalWrite(AIN2,LOW);

    digitalWrite(BIN1,LOW);

    digitalWrite(BIN2,LOW);

    digitalWrite(5,HIGH);

}


void loop() {

 

    // if programming failed, don't try to do anything

    if (!dmpReady) return;


    // wait for MPU interrupt or extra packet(s) available

    while (!mpuInterrupt && fifoCount < packetSize)

    {

        //no mpu data - performing PID calculations and output to motors     

        pid.Compute();   

        

        //Print the value of Input and Output on serial monitor to check how it is working.

       // Serial.print(input); Serial.print(" =>"); Serial.println(output);
             

        if (input>165 && input<215){//If the Bot is falling 

          

        if (output>0) //Falling towards front 

        Forward(); //Rotate the wheels forward 

        else if (output<0) //Falling towards back

        Reverse(); //Rotate the wheels backward 

        }

        else //If Bot not falling

        Stop(); //Hold the wheels still

        

    }


    // reset interrupt flag and get INT_STATUS byte

    mpuInterrupt = false;

    mpuIntStatus = mpu.getIntStatus();


    // get current FIFO count

    fifoCount = mpu.getFIFOCount();


    // check for overflow (this should never happen unless our code is too inefficient)

    if ((mpuIntStatus & 0x10) || fifoCount == 1024)

    {

        // reset so we can continue cleanly

        mpu.resetFIFO();

       // Serial.println(F("FIFO overflow!"));


    // otherwise, check for DMP data ready interrupt (this should happen frequently)

    }

    else if (mpuIntStatus & 0x02)

    {

        // wait for correct available data length, should be a VERY short wait

        while (fifoCount < packetSize) fifoCount = mpu.getFIFOCount();


        // read a packet from FIFO

        mpu.getFIFOBytes(fifoBuffer, packetSize);

        

        // track FIFO count here in case there is > 1 packet available

        // (this lets us immediately read more without waiting for an interrupt)

        fifoCount -= packetSize;


        mpu.dmpGetQuaternion(&q, fifoBuffer); //get value for q

        mpu.dmpGetGravity(&gravity, &q); //get value for gravity

        mpu.dmpGetYawPitchRoll(ypr, &q, &gravity); //get value for ypr


        input = ypr[1] * 180/M_PI + 180;

   }

}


void Forward() //Code to rotate the wheel forward 

{

    digitalWrite(AIN1,HIGH); //Motor A Rotate Clockwise
    digitalWrite(AIN2,LOW);
    digitalWrite(BIN1,LOW); //Motor B Rotate AntiClockwise
    digitalWrite(BIN2,HIGH);
    
    analogWrite(PWM1,output); //Speed control of Motor A
    analogWrite(PWM2,output); //Speed control of Motor B

   // Serial.print("F"); //Debugging information 

}


void Reverse() //Code to rotate the wheel Backward  

{

  digitalWrite(AIN1,LOW); //Motor A Rotate AntiClockwise
  digitalWrite(AIN2,HIGH);
  digitalWrite(BIN1,HIGH); //Motor B Rotate Clockwise
  digitalWrite(BIN2,LOW);
  
  analogWrite(PWM1,output*-1); //Speed control of Motor A
  analogWrite(PWM2,output*-1); //Speed control of Motor B

 // Serial.print("R");

}


void Stop() //Code to stop both the wheels

{
    digitalWrite(AIN1,LOW);
    digitalWrite(AIN2,LOW);
    digitalWrite(BIN1,LOW);
    digitalWrite(BIN2,LOW);
    
    analogWrite(PWM1,0); //Speed control of Motor A
    analogWrite(PWM2,0); //Speed control of Motor B
    
  //  Serial.print("S");

}

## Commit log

2023-07-08 Working PID
    [LeftWheelLink.STL, RightWheelLink.STL, base_link.STL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]
2023-07-08 Update with CAD files, Simscape Simulation and Arduino Nano code
    [LeftWheelLink.STL, Motor_mount.SLDPRT, RightWheelLink.STL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]
